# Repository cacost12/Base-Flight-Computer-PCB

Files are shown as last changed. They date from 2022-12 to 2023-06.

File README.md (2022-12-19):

<h1>Flight Computer Lite</h1>

<p><b>Current PCB Revision:</b> 1.0</p>
<p><b>PCB Part Number:</b> A0007</p>

<p>The Avionics team aims to produce a dual-deploy flight computer 
 for use in high powered rocketry projects. The Avionics
flight computer PCB uses an ARM Microcontroller to provide a 
computationally capable embedded protoyping 
platform for high powered rocketry projects with minimal wiring and a small
 form factor.</p>

<b>Working Directory Structure:</b>
 
 <p>
doc: documentation
    
src: source design files, e.g. schematic and board files
 
lib: libraries for schematic symbols and footprints
 
production: files needed for pcb fabrication, e.g. gerbers, profile, drill file
 
 sim: simulation files 
  
 cad: 3d models
   
 img: images of circuit/footprints for github display 
 </p>

<h2>3D Model: </h2>

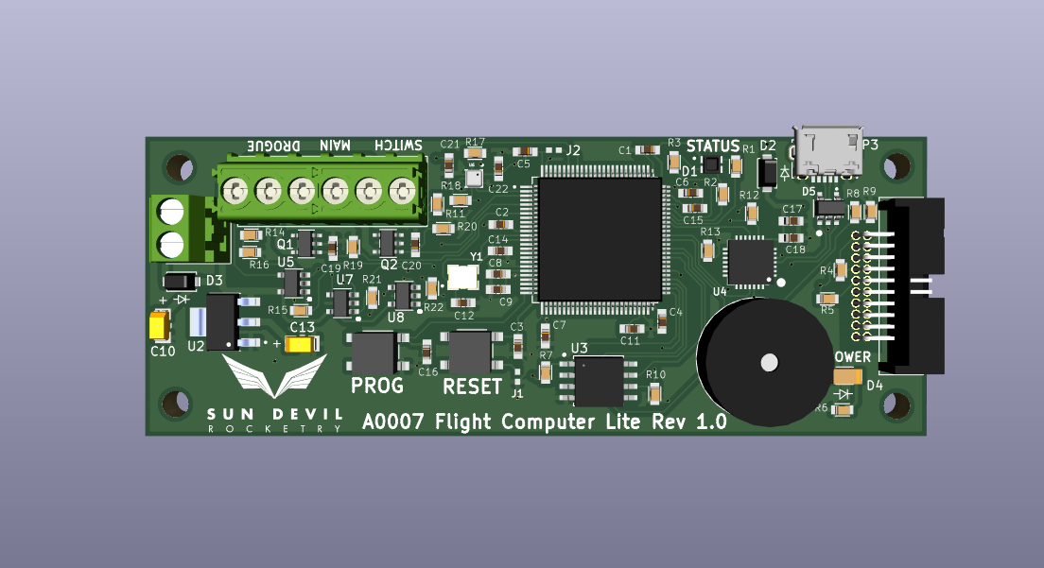
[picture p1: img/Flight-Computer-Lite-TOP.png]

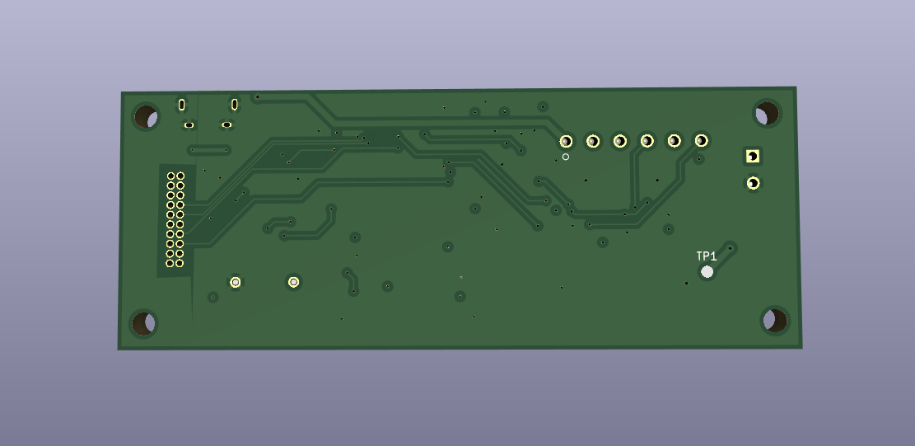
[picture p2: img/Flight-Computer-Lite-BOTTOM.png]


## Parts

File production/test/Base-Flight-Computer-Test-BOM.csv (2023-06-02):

Id | Designator | Footprint | Quantity | Designation | Supplier and ref
1 | R20,R8,R3,R9 | RES_0402 | 4 | 100k
2 | C6,C7,C5 | CAP_0402 | 3 | 1uF
3 | D1 | CLMVC-FKA-CL1D1L71BB7C3C3 | 1 | CLMVC-FKA-CL1D1L71BB7C3C3
4 | H4,H3,H1,H2 | MountingHole_4-40 | 4 | Mounting-Hole-4-40
5 | P3 | 53047-0610 | 1 | 0530470610
6 | C8,C1,C9,C2 | CAP_0402 | 4 | 0.1uF
7 | R13,R12 | RES_0402 | 2 | 4.7k
8 | D2,D5,D4 | PMEG3010AESBYL | 3 | PMEG3010AESBYL
9 | BZ1 | AT-1438-TWT-R | 1 | AT-1438-TWT-R
10 | R4,R5 | RES_0402 | 2 | 82
11 | R1,R22,R7,R19,R17,R18 | RES_0402 | 6 | 10k
12 | P5 | B2B-PH-K-SLFSN_JST | 1 | B2B-PH-K-SLFSN_JST
13 | Q2,Q3,Q5,Q6 | 2N7002W-7-F | 4 | 2N7002W-7-F
14 | C4 | CAP_0402 | 1 | 10nF
15 | P2 | 10118194-0001LF | 1 | USB
16 | J1 | Jumper-NO | 1 | Jumper_NO
17 | U3 | AP7370-33Y-13 | 1 | LMS8117AMP-3.3_NOPB
18 | R21 | RES_0402 | 1 | 39k
19 | U2 | BMP390 | 1 | BMP390
20 | Q4,Q1 | QS5U17TR | 2 | QS5U17TR
21 | Y1 | ECS-240-12-37B-CKY-TR | 1 | ECS-240-18-33-JGN-TR
22 | C11,C10 | CAP_0402 | 2 | 4pF
23 | R6,R16 | RES_0402 | 2 | 240
24 | C3 | CAP_0402 | 1 | 4.7uF
25 | C13,C12 | CAP_0603 | 2 | 1uF
26 | D3 | LTST-C191KGKT | 1 | LTST-C191KGKT
27 | P1,P4 | 1546551-4 | 2 | 1984659
28 | U4 | SST25VF040B-50-4I-S2AE-T | 1 | SST25VF040B-50-4I-S2AE-T
29 | R11 | RES_0402 | 1 | 200k
30 | U1 | STM32G4A1KEU6 | 1 | STM32G4A1KEU6

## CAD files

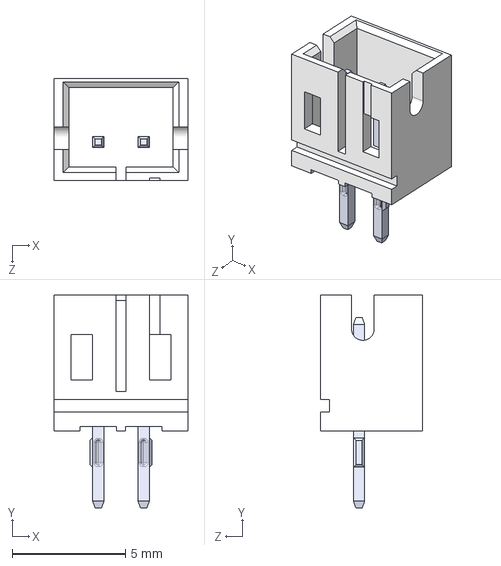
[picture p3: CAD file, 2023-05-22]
CAD/3Dfiles/B2B_PH_K_S_LF__SN_.step
5.90 x 9.40 x 4.50 mm

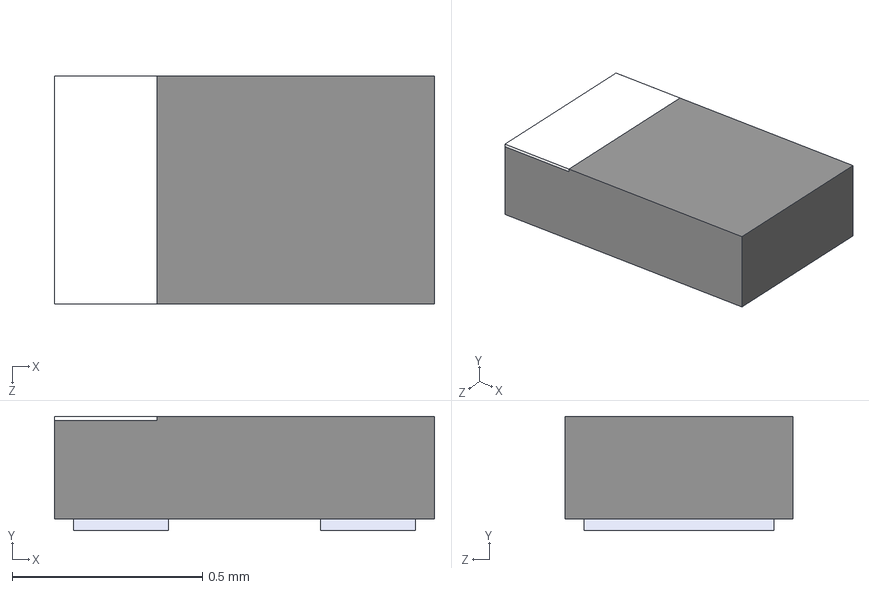
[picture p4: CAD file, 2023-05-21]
CAD/3Dfiles/PMEG3010AESBYL.step
1.00 x 0.3 x 0.6 mm

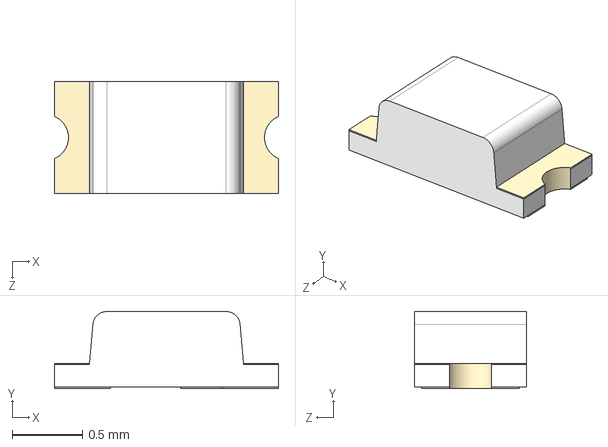
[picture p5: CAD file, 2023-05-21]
CAD/3Dfiles/LTST-C191KGKT.step
1.60 x 0.55 x 0.8 mm

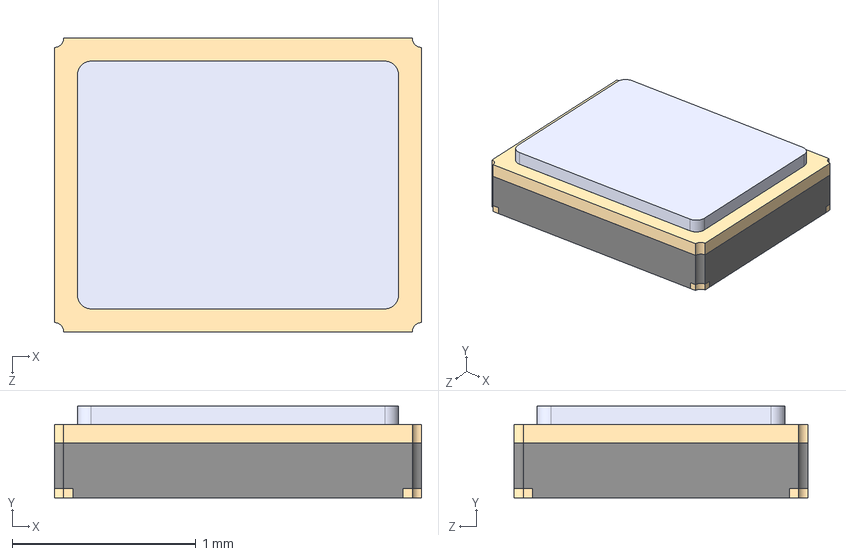
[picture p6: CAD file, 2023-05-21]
CAD/3Dfiles/ECS-240-12-37B-CKY-TR.step
2.00 x 0.5 x 1.60 mm

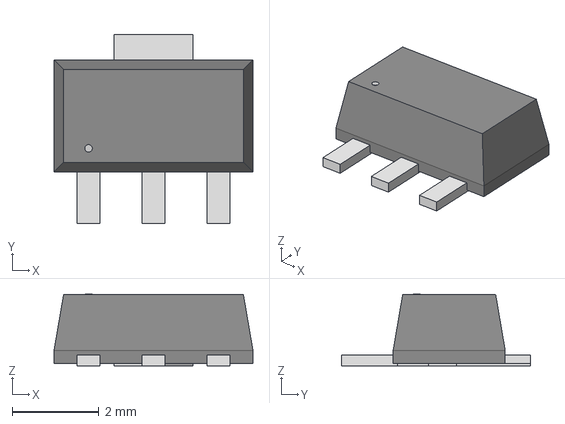
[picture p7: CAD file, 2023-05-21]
CAD/3Dfiles/AP7370-33Y-13.step
4.60 x 4.37 x 1.65 mm

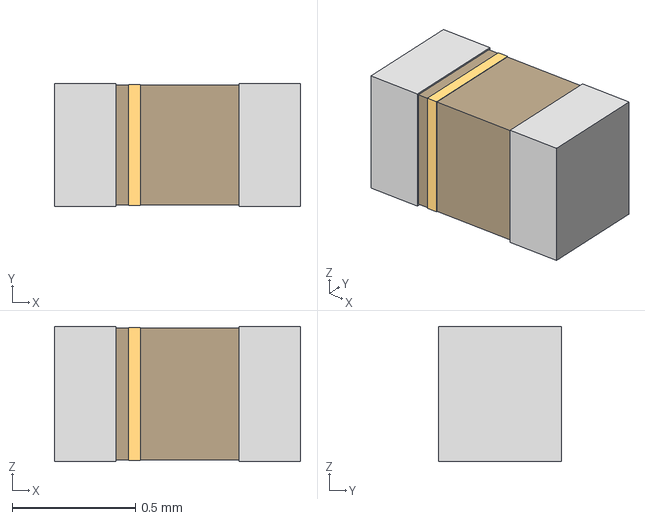
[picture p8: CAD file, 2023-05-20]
CAD/3Dfiles/CAP_0402.step
1.00 x 0.5 x 0.55 mm

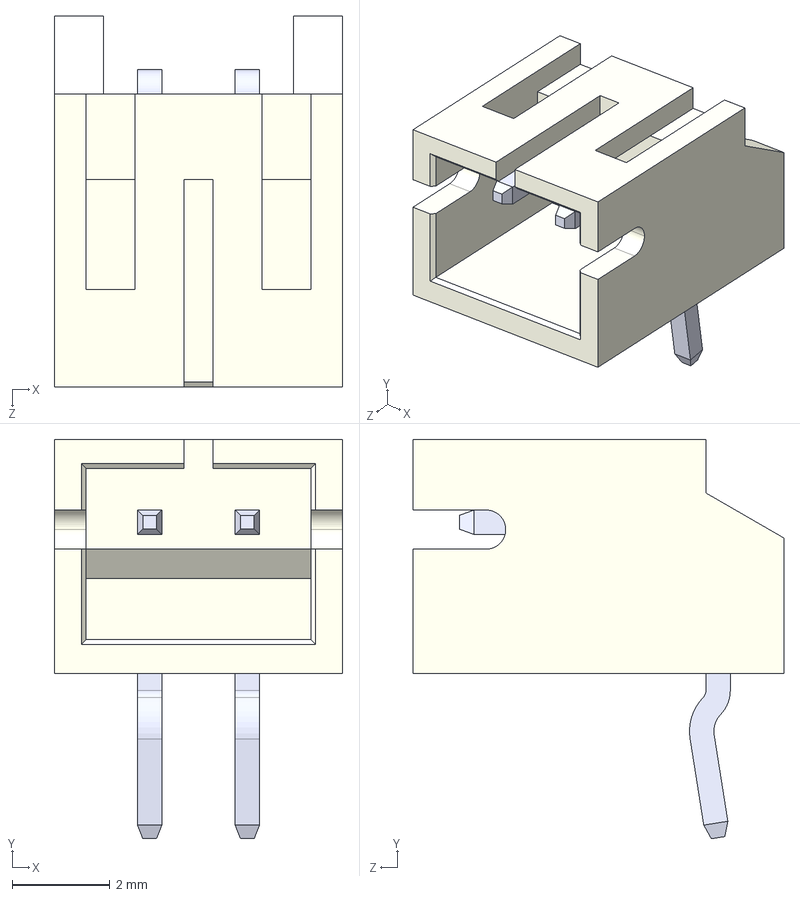
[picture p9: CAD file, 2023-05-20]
CAD/3Dfiles/S2B-PH-K-S_LF__SN_.step
5.90 x 8.18 x 7.60 mm

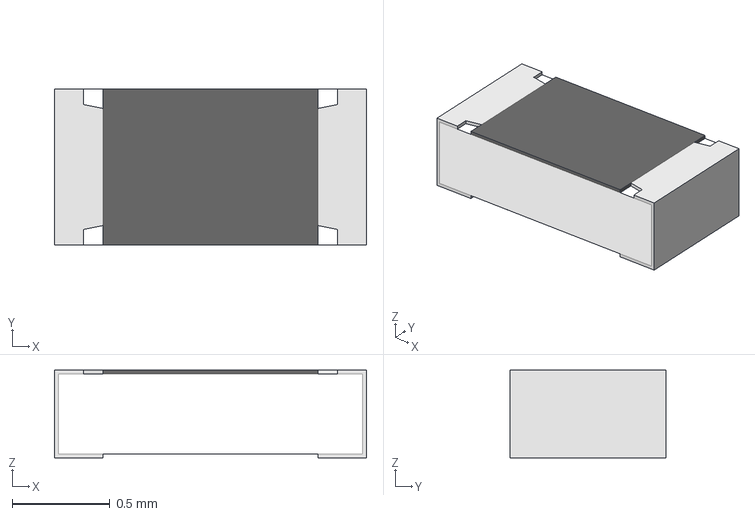
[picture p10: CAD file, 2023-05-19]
CAD/3Dfiles/RES_0603.step
1.60 x 0.8 x 0.45 mm

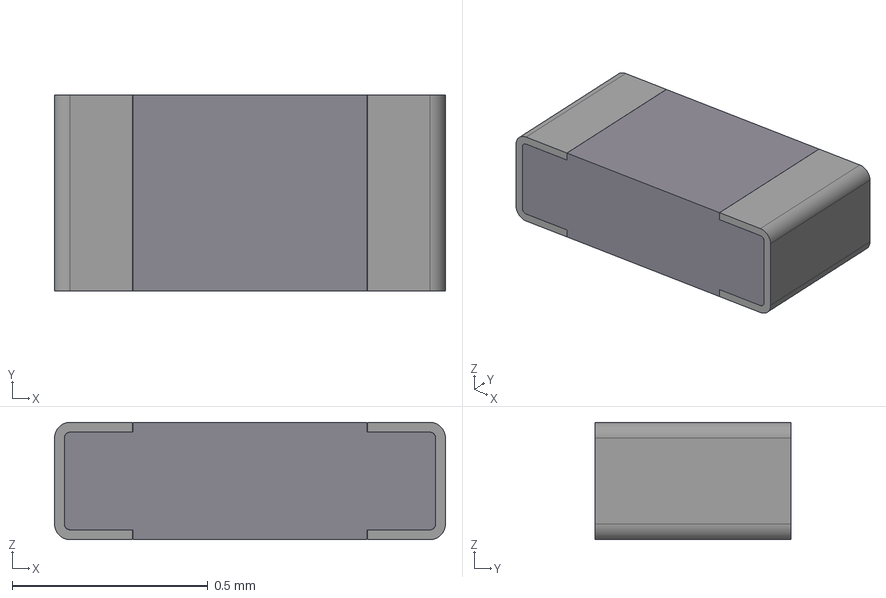
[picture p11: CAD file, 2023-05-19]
CAD/3Dfiles/RES_0402.step
1.00 x 0.5 x 0.3 mm
Chip_001

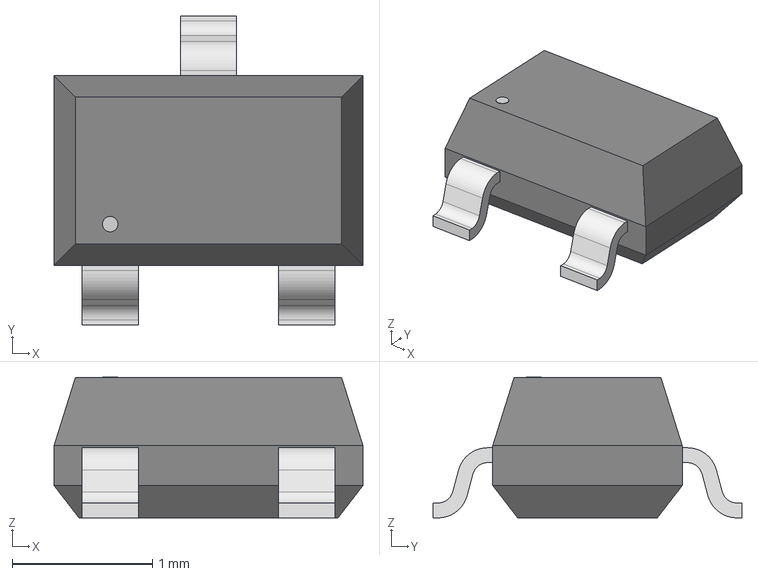
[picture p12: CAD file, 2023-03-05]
CAD/3Dfiles/2N7002W-7-F.step
2.20 x 2.20 x 1.00 mm

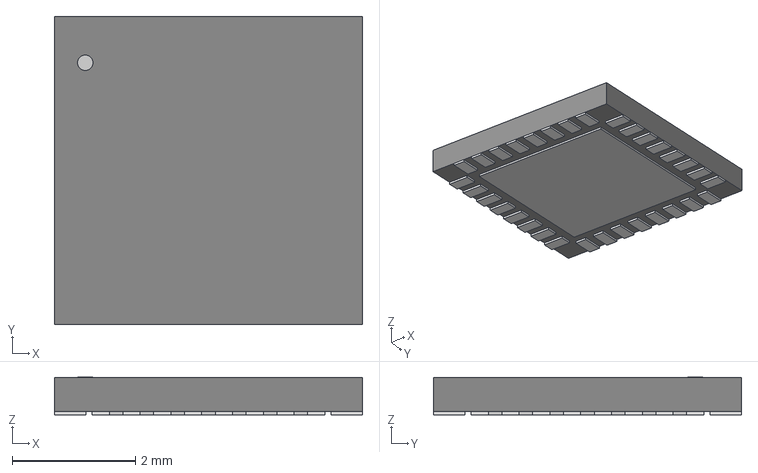
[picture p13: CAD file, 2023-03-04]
CAD/3Dfiles/stm32g4a1keu6.step
5.00 x 5.00 x 0.612 mm

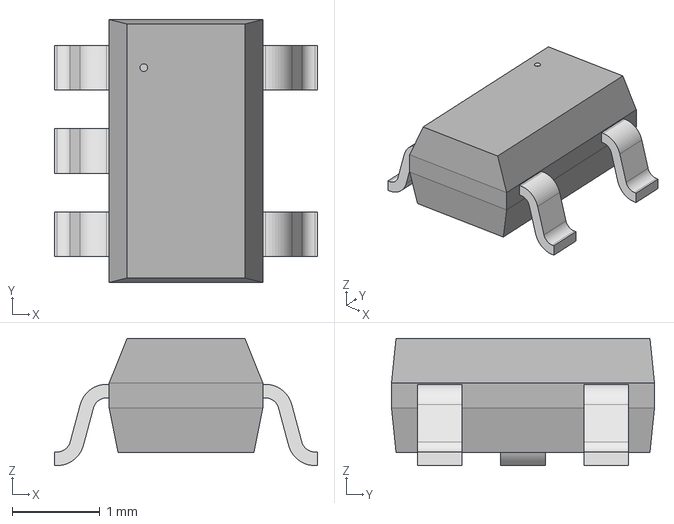
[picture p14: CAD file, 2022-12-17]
CAD/3Dfiles/TS391lYLT.step
3.00 x 3.00 x 1.45 mm

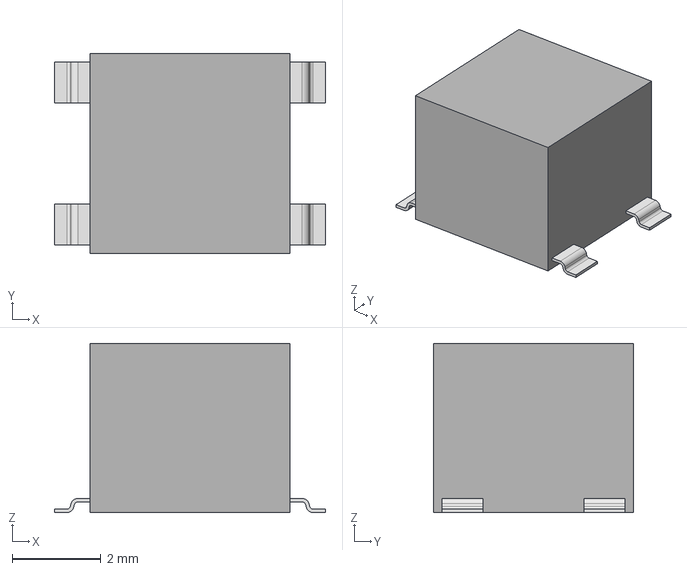
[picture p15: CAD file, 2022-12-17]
CAD/3Dfiles/PTS647SM38SMTR2LFS.step
6.10 x 4.50 x 3.81 mm

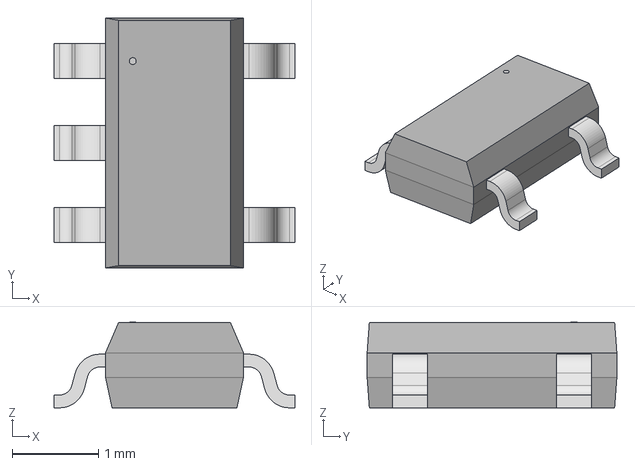
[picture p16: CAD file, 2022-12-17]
CAD/3Dfiles/QS5U17TR.step
2.79 x 2.90 x 0.993 mm

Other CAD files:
CAD/3Dfiles/CP2102-GMR_QFN28.step
CAD/3Dfiles/CLMVC-FKA-CL1D1L71BB7C3C3.STEP
CAD/3Dfiles/SP0504BAHTG.step
CAD/3Dfiles/AT-1438-TWT-R.STEP
CAD/3Dfiles/10118194-0001LF.step
CAD/3Dfiles/1546551-2.step
CAD/3Dfiles/1546551-4.step
CAD/3Dfiles/284391-6.step
CAD/3Dfiles/530470610.stp
CAD/3Dfiles/BMP390.STEP
CAD/3Dfiles/CAP_0603.step
CAD/3Dfiles/SM5819PL-TP.step
CAD/3Dfiles/SST25VF040B-50-4I-S2AE-T.step
CAD/3Dfiles/T491A106K010AT.step

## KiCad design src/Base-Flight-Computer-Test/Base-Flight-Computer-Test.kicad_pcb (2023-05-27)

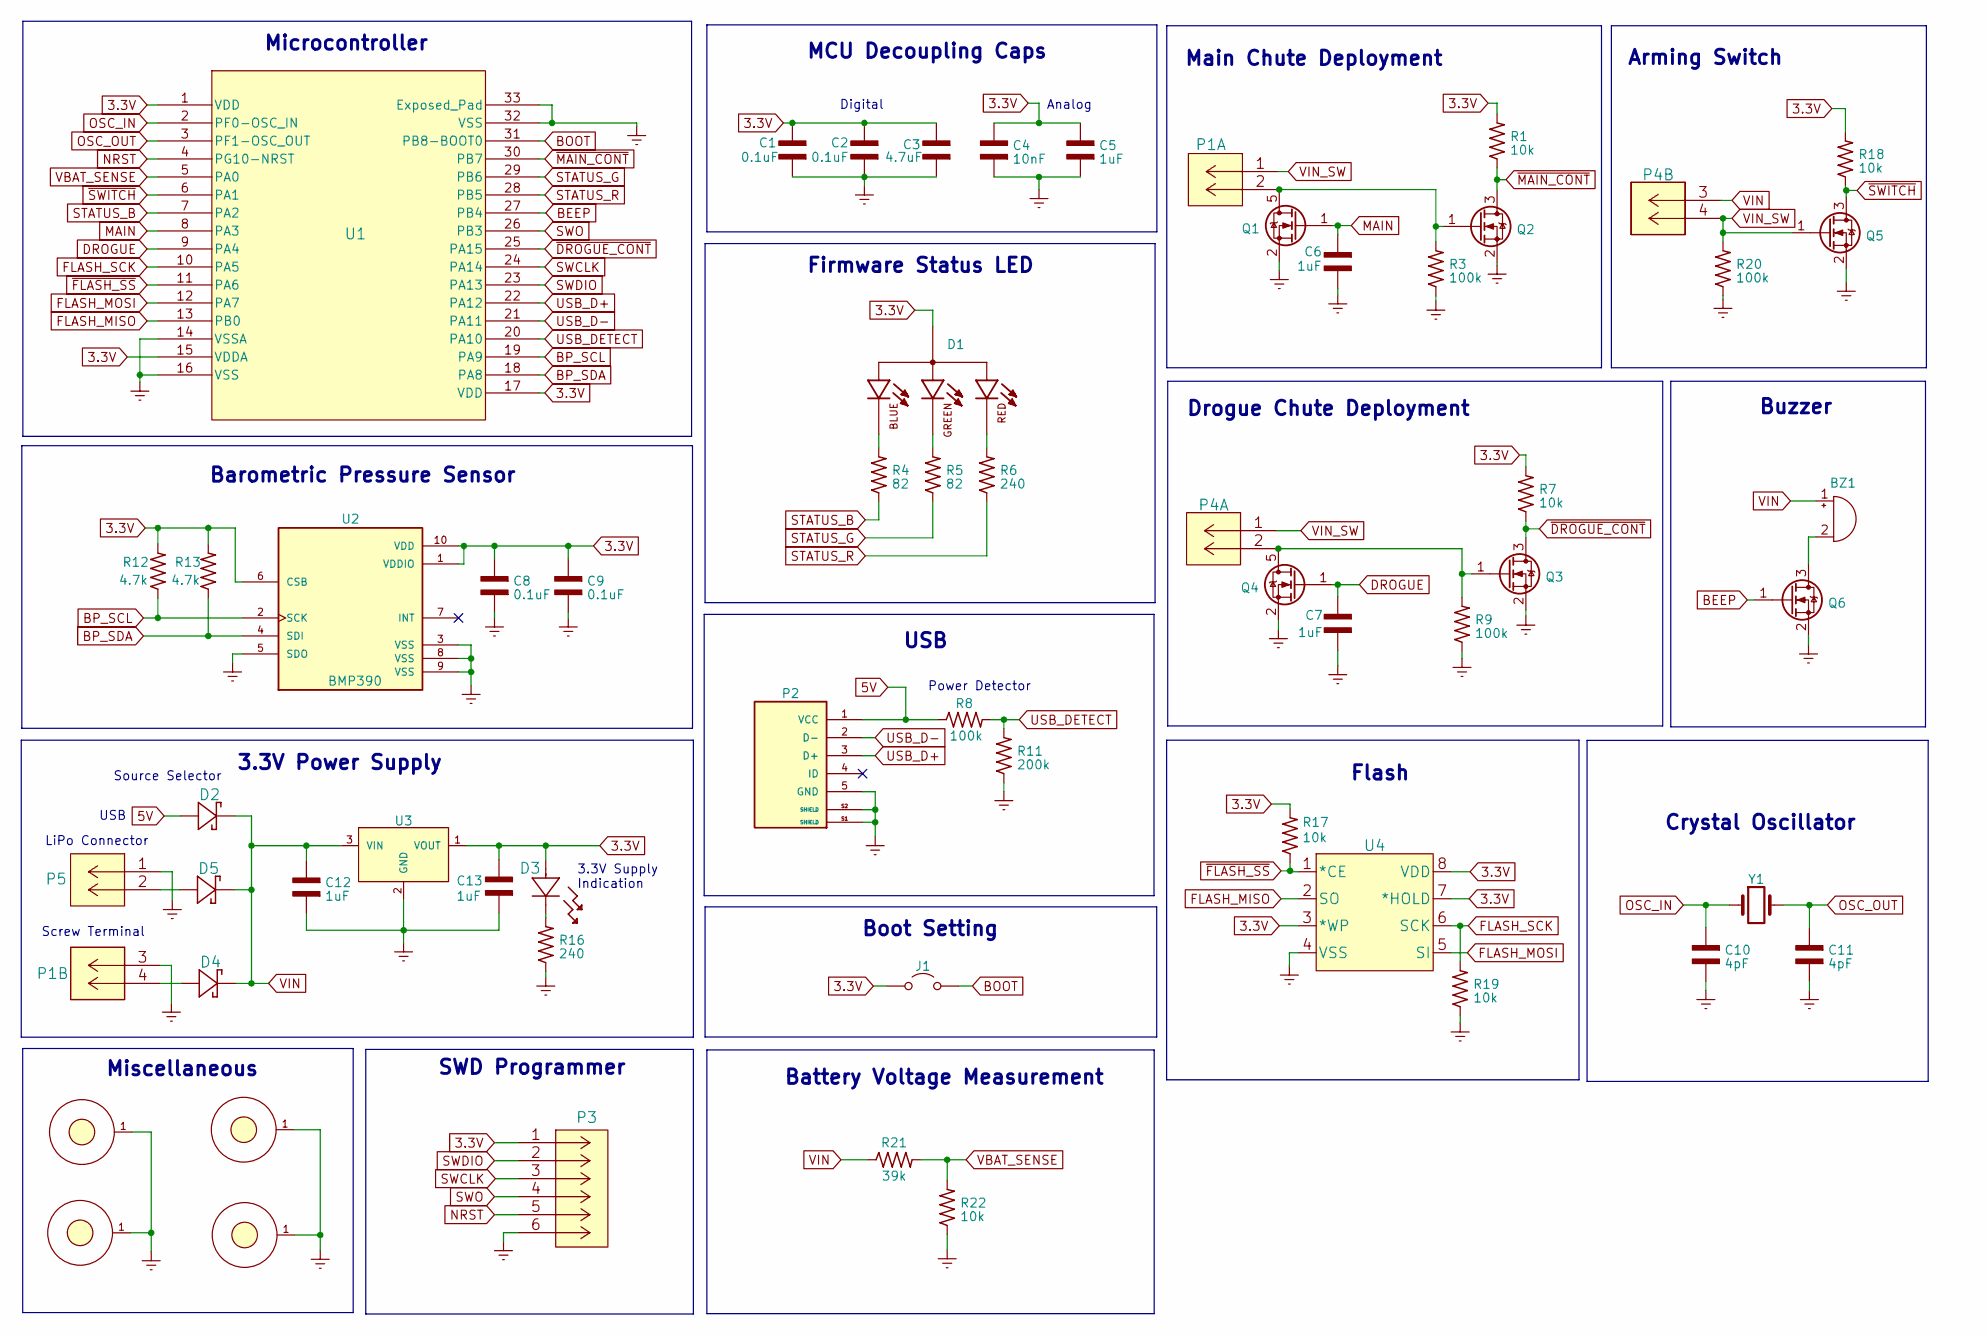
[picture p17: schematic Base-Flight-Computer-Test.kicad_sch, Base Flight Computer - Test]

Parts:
BZ1: AT-1438-TWT-R
C1, C2, C8, C9: 0.1uF; CAP_0402
C3: 4.7uF; CAP_0402
C4: 10nF; CAP_0402
C5, C6, C7: 1uF; CAP_0402
C10, C11: 4pF; CAP_0402
C12, C13: 1uF; CAP_0603
D1: CLMVC-FKA-CL1D1L71BB7C3C3
D2, D4, D5: PMEG3010AESBYL
D3: LTST-C191KGKT
H1, H2, H3, H4: Mounting-Hole-4-40; MountingHole_4-40
J1: Jumper_NO; Jumper-NO
P1, P4: 1984659; 1546551-4
P2: USB; 10118194-0001LF
P3: 0530470610; 53047-0610
P5: B2B-PH-K-SLFSN_JST
Q1, Q4: QS5U17TR
Q2, Q3, Q5, Q6: 2N7002W-7-F
R1, R7, R17, R18, R19, R22: 10k; RES_0402
R3, R8, R9, R20: 100k; RES_0402
R4, R5: 82; RES_0402
R6, R16: 240; RES_0402
R11: 200k; RES_0402
R12, R13: 4.7k; RES_0402
R21: 39k; RES_0402
U1: STM32G4A1KEU6
U2: BMP390
U3: LMS8117AMP-3.3_NOPB; AP7370-33Y-13
U4: SST25VF040B-50-4I-S2AE-T
Y1: ECS-240-18-33-JGN-TR; ECS-240-12-37B-CKY-TR

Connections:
3.3V: C1.1, C2.1, C3.1, C4.1, C5.1, C8.1, C9.1, C13.1, D1.1, D3.2, J1.1 (A), P3.1, R1.2, R7.2, R12.2, R13.2, R17.2, R18.2, U1.1 (VDD), U1.15 (VDDA), U1.17 (VDD), U2.1 (VDDIO), U2.6 (CSB), U2.10 (VDD), U3.1 (VOUT), U4.3 (*WP), U4.7 (*HOLD), U4.8 (VDD)
5V: D2.A, P2.1 (VCC), R8.1
BEEP: Q6.1 (G), U1.27 (PB4)
BOOT: J1.2 (B), U1.31 (PB8-BOOT0)
BP_SCL: R12.1, U1.19 (PA9), U2.2 (SCK)
BP_SDA: R13.1, U1.18 (PA8), U2.4 (SDI)
DROGUE: C7.1, Q4.1 (G), U1.9 (PA4)
Earth: C1.2, C2.2, C3.2, C4.2, C5.2, C6.2, C7.2, C8.2, C9.2, C10.2, C11.2, C12.2, C13.2, H1.1, H2.1, H3.1, H4.1, P1.3 (5), P2.5 (GND), P2.S1 (SHIELD), P2.S2 (SHIELD), P3.6, P5.1 (5), Q1.2 (S), Q2.2 (S), Q3.2 (S), Q4.2 (S), Q5.2 (S), Q6.2 (S), R3.1, R9.1, R11.1, R16.1, R19.1, R20.1, R22.1, U1.14 (VSSA), U1.16 (VSS), U1.32 (VSS), U1.33 (Exposed_Pad), U2.3 (VSS), U2.5 (SDO), U2.8 (VSS), U2.9 (VSS), U3.2 (GND), U4.4 (VSS)
FLASH_MISO: U1.13 (PB0), U4.2 (SO)
FLASH_MOSI: U1.12 (PA7), U4.5 (SI)
FLASH_SCK: R19.2, U1.10 (PA5), U4.6 (SCK)
MAIN: C6.1, Q1.1 (G), U1.8 (PA3)
NRST: P3.5, U1.4 (PG10-NRST)
unnamed: BZ1.2 (+), Q6.3 (D)
unnamed: D1.2, R4.2
unnamed: D1.3, R5.2
unnamed: D1.4, R6.2
unnamed: D3.1, R16.2
unnamed: P1.2 (6), Q1.5 (D), Q2.1 (G), R3.2
unnamed: D4.A, P1.4 (6)
unnamed: P4.2 (6), Q3.1 (G), Q4.5 (D), R9.2
unnamed: D5.A, P5.2 (6)
OSC_IN: C10.1, U1.2 (PF0-OSC_IN), Y1.1
OSC_OUT: C11.1, U1.3 (PF1-OSC_OUT), Y1.3
STATUS_B: R4.1, U1.7 (PA2)
STATUS_G: R5.1, U1.29 (PB6)
STATUS_R: R6.1, U1.28 (PB5)
SWCLK: P3.3, U1.24 (PA14)
SWDIO: P3.2, U1.23 (PA13)
SWO: P3.4, U1.26 (PB3)
USB_D+: P2.3 (D+), U1.22 (PA12)
USB_D-: P2.2 (D-), U1.21 (PA11)
USB_DETECT: R8.2, R11.2, U1.20 (PA10)
VBAT_SENSE: R21.2, R22.2, U1.5 (PA0)
VIN: BZ1.1 (-), C12.1, D2.C, D4.C, D5.C, P4.3 (5), R21.1, U3.3 (VIN)
VIN_SW: P1.1 (5), P4.1 (5), P4.4 (6), Q5.1 (G), R20.2
~DROGUE_CONT: Q3.3 (D), R7.1, U1.25 (PA15)
~FLASH_SS: R17.1, U1.11 (PA6), U4.1 (*CE)
~MAIN_CONT: Q2.3 (D), R1.1, U1.30 (PB7)
~SWITCH: Q5.3 (D), R18.1, U1.6 (PA1)

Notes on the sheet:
MCU Decoupling Caps
Drogue Chute Deployment
Flash
Digital
USB
Source Selector
Analog
Barometric Pressure Sensor
LiPo Connector
3.3V Supply Indication
Miscellaneous
Boot Setting
3.3V Power Supply
Main Chute Deployment
Firmware Status LED
Battery Voltage Measurement
Screw Terminal
Arming Switch
SWD Programmer
Buzzer
Microcontroller
Power Detector
Crystal Oscillator

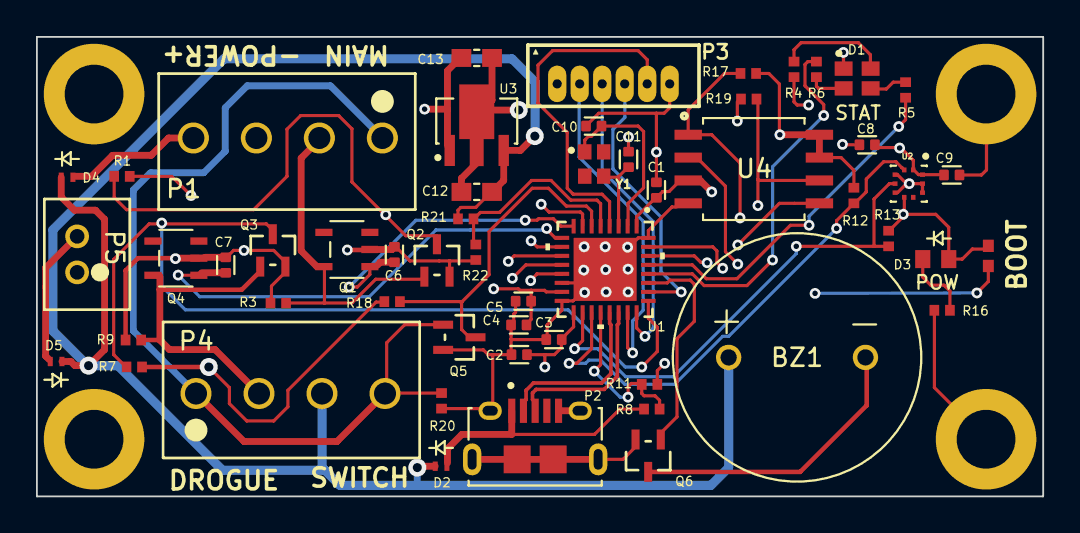
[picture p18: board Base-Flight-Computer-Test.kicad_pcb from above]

Board: 4 copper layers, 55.9 x 25.5 mm, 58 parts (0 on the bottom side), 40 nets.

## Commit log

2022-12-17 created initial footprint library
    [10118194-0001LF.step, 1546551-2.step, 3220-20-0200-00.stp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]
2022-12-17 created initial component symbol library
    [TS391lYLT.step]
2022-12-17 completed schematic
    [Flight-Computer-Lite.kicad_sch, Peripherals.kicad_sch]
2022-12-18 imported footprints into layout
    [Flight-Computer-Lite.kicad_pcb, Flight-Computer-Lite.kicad_sch, Peripherals.kicad_sch]
2022-12-18 finalized board outline and component placements
    [Flight-Computer-Lite.kicad_pcb, Flight-Computer-Lite.kicad_sch, Peripherals.kicad_sch]
2022-12-19 finalized rev1 routing
    [Flight-Computer-Lite.kicad_pcb, Flight-Computer-Lite.kicad_sch]
2022-12-19 resolved DRC errors
    [Flight-Computer-Lite.kicad_pcb]
2022-12-19 generated gerbers files
    [Flight-Computer-Lite-B_Cu.gbr, Flight-Computer-Lite-B_Mask.gbr, Flight-Computer-Lite-B_Paste.gbr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]
2022-12-19 added PCB images to readme
2022-12-20 added ignition continuity pull down resistors to schematic
    [Flight-Computer-Lite.kicad_pcb, Flight-Computer-Lite.kicad_sch, Peripherals.kicad_sch]
2022-12-21 added ignition pull down resistors to layout
    [Flight-Computer-Lite-B_Cu.gbr, Flight-Computer-Lite-B_Mask.gbr, Flight-Computer-Lite-B_Paste.gbr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]
2023-02-01 reduced form factor
    [Flight-Computer-Lite.kicad_pcb, Flight-Computer-Lite.kicad_sch]
2023-02-02 re-routed PCB to smaller form factor
    [Flight-Computer-Lite.kicad_pcb]
2023-02-02 generated fabrication outputs
    [Flight-Computer-Lite-B_Cu.gbr, Flight-Computer-Lite-B_Mask.gbr, Flight-Computer-Lite-B_Paste.gbr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]
2023-02-06 kicad backups
2023-03-04 added new mcu to lib files
    [stm32g4a1keu6.step]
2023-03-05 created rev2 schematic
    [2N7002W-7-F.step, 530470610.stp, Flight-Computer-Lite.kicad_sch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]
2023-03-05 placed rev2 components on board
    [Flight-Computer-Lite.kicad_pcb]
2023-03-23 began PCB routing
    [Flight-Computer-Lite.kicad_pcb]
2023-03-24 finished initial routing
    [Flight-Computer-Lite.kicad_pcb]
2023-05-19 removed programming button
    [Base-Flight-Computer.kicad_pcb, Base-Flight-Computer.kicad_sch, Peripherals.kicad_sch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]
2023-05-19 increased blue LED resistance
    [Base-Flight-Computer.kicad_sch]
2023-05-19 added 0402 resistor to component symbol library
2023-05-19 created new footprint library
2023-05-19 added 0402 resistor to footprint library
    [RES_0402.step]
2023-05-19 updated footprint library
    [RES_0603.step]
2023-05-19 added 4-40 screw mounting hole to component libraries
2023-05-20 linked all component symbols to footprints
2023-05-20 updated schematic links to new library files
    [Base-Flight-Computer.kicad_sch, Sheet2.kicad_sch]
2023-05-20 added new 6 terminal screw terminal to lib files
    [284391-6.step]
2023-05-20 added new screw terminals to schematic
    [Base-Flight-Computer.kicad_sch, Sheet2.kicad_sch]
2023-05-20 added LiPo connector to lib files
    [S2B-PH-K-S_LF__SN_.step]
2023-05-20 added 0402 capacitor to lib files
    [CAP_0402.step]
2023-05-20 updated schematic with 0402 resistors and capacitors
    [Base-Flight-Computer.kicad_sch, Sheet2.kicad_sch]
2023-05-20 added battery measurement circuit
    [Base-Flight-Computer.kicad_sch, Sheet2.kicad_sch]
2023-05-20 added new linear regulator to lib files
    [NCP176AMX330TCG.step]
2023-05-21 swapped out linear regulator for reduced form factor
    [AP7370-33Y-13.step, Base-Flight-Computer.kicad_sch, LMS8117AMP-3.3_NOPB.step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]
2023-05-21 removed extra units from JST connector symbol
    [Base-Flight-Computer.kicad_sch]
2023-05-21 added lipo batter connector to power supply circuit
    [Base-Flight-Computer.kicad_sch]
2023-05-21 reduced form factor of crystal oscillator
    [Base-Flight-Computer.kicad_sch, ECS-240-12-37B-CKY-TR.step, ECS-240-18-33-JGN-TR.STEP]
2023-05-21 changed ignition pull-down resistors to 100k to reduce parasitic ematch current
    [Base-Flight-Computer.kicad_sch]
2023-05-21 moved all components to single schematic page
    [Base-Flight-Computer.kicad_sch, Sheet2.kicad_sch]
2023-05-21 updated symbol footprint links in schematic
    [3220-20-0200-00.stp, Base-Flight-Computer.kicad_sch]
2023-05-21 added four terminal screw terminal to lib files
    [1546551-4.step, Base-Flight-Computer.kicad_pcb, Base-Flight-Computer.kicad_sch]
2023-05-21 replaced green power indication LED with smaller 0603 alternate
    [Base-Flight-Computer.kicad_pcb, Base-Flight-Computer.kicad_sch, LTST-C191KGKT.step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]
2023-05-21 replaced schottky diode with smaller form factor diode
    [Base-Flight-Computer.kicad_pcb, Base-Flight-Computer.kicad_sch, PMEG3010AESBYL.step]
2023-05-22 swapped out 90 degree LiPo connector for straight connector
    [B2B_PH_K_S_LF__SN_.step, Base-Flight-Computer.kicad_pcb, Base-Flight-Computer.kicad_sch]
2023-05-24 finished placing components on board
    [Base-Flight-Computer.kicad_pcb]
2023-05-26 created new project for preliminary hardware testing
    [Base-Flight-Computer-Test.kicad_pcb, Base-Flight-Computer-Test.kicad_sch, Base-Flight-Computer.kicad_pcb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]
2023-05-26 placed components on test board
    [Base-Flight-Computer-Test.kicad_pcb]
2023-05-26 updated DRC ruleset
    [Base-Flight-Computer-Test.kicad_pcb]
2023-05-26 completed initial test layout
    [Base-Flight-Computer-Test.kicad_pcb, Base-Flight-Computer-Test.kicad_sch]
2023-05-27 resolved DRC issues with Test layout
    [Base-Flight-Computer-Test.kicad_pcb]
2023-05-27 generated test board gerber files
    [Base-Flight-Computer-Test-B_Cu.gbr, Base-Flight-Computer-Test-B_Mask.gbr, Base-Flight-Computer-Test-B_Paste.gbr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]
2023-05-27 plotted schematic
    [Base-Flight-Computer-Test.kicad_pcb, Base-Flight-Computer-Test.kicad_sch]
2023-06-02 organized production folder and generated BOM
    [Base-Flight-Computer-Test-BOM.csv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]
